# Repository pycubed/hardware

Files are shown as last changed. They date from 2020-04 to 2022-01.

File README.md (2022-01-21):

# Hardware ⚙
<br><br>
<p align="middle">
  
</p><br>

## [All PyCubed Resources](https://www.notion.so/maholli/All-PyCubed-Resources-8738cab0dd0743239a3cde30c6066452)
Tutorials, design resources, and more!
<br>

## Details:
- 4-layer PCB, minimum trace/spacing > 8 mils.
- Can be fabricated using standard FR4 for prototypes and Isola FR408HR for flight.
  - 50 ohm controlled impedance design spec'd for FR408HR with 11 mils external and 10.7 mils interal trace widths.
  - See [PyCubed's 2019 SmallSat Paper](https://github.com/pycubed/documentation/blob/master/PyCubed_smallsat-paper.pdf) for more discussion on the stack-up.
- Zipped, ready-to-order, gerber files can be found in the root of each revision directory. 
- NOTE: PyCubed layout has been ported from Eagle to KiCad to maintain the open-source nature of the project. Visit [http://www.kicad.org/](http://www.kicad.org/) for more details on this layout tool.
<br>

## Change Log
- [mainboard-v04 ➡ mainboard-v05](https://pycubed.org/v04-v05-Change-Log-7d80b1fb81be423a9da197f820e87538)
<br>

## Interactive Bill of Materials 🛒
- [mainboard-v01](https://pycubed.github.io/hardware/mainboard-v01)
- [mainboard-v02](https://pycubed.github.io/hardware/mainboard-v02)
- [mainboard-v04](https://pycubed.github.io/hardware/mainboard-v04)
- [mainboard-v05](https://pycubed.github.io/hardware/mainboard-v05)
<br>
<br>
<br>
<br>
<br>
<br>

## License
<br />
- Hardware in this repository is licensed under a <a rel="license" href="http://creativecommons.org/licenses/by-sa/4.0/">Creative Commons Attribution-ShareAlike 4.0 International License</a>.
- Software/firmware in this repository is licensed under MIT unless otherwise indicated.

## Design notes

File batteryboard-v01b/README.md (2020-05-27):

# PyCubed Battery Board 🔋

## [⭐ See the PyCubed Battery page for more details](https://www.notion.so/maholli/PyCubed-4cbfac7e9b684852a2ab2193bd485c4d)

<p align="middle">
  
</p>

2S3P Li-ion battery pack for CubeSat designs.
   - Fits 18650 cells (like the LG INR18650-MJ1)
   - Meets maximum capacity requirements of common CubeSat integrators
   - Uses components with radiation testing heritage
      - R5460x2xx for protection against
         - over-charge 
         - over-discharge
         - short-circuit
         - excess discharge-current
         - excess charge-current

Tested against the following flight requirement documents:
(the cells you use play a big role here)
   - TBA

## Interactive Bill of Materials 🛒
- [batteryboard-v01](https://pycubed.github.io/hardware/batteryboard-v01)

This board is merely a starting point for your spacecraft. Always follow the requirements set forth by your launch provider and integrator.

<br>
<br>
<br>
<br />This work is licensed under a <a rel="license" href="http://creativecommons.org/licenses/by/4.0/">Creative Commons Attribution 4.0 International License</a>.

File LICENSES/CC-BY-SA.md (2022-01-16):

Creative Commons Attribution-ShareAlike 4.0 International

Creative Commons Corporation ("Creative Commons") is not a law firm and does not provide legal services or legal advice. Distribution of Creative Commons public licenses does not create a lawyer-client or other relationship. Creative Commons makes its licenses and related information available on an "as-is" basis. Creative Commons gives no warranties regarding its licenses, any material licensed under their terms and conditions, or any related information. Creative Commons disclaims all liability for damages resulting from their use to the fullest extent possible.

Using Creative Commons Public Licenses

Creative Commons public licenses provide a standard set of terms and conditions that creators and other rights holders may use to share original works of authorship and other material subject to copyright and certain other rights specified in the public license below. The following considerations are for informational purposes only, are not exhaustive, and do not form part of our licenses.

Considerations for licensors: Our public licenses are intended for use by those authorized to give the public permission to use material in ways otherwise restricted by copyright and certain other rights. Our licenses are irrevocable. Licensors should read and understand the terms and conditions of the license they choose before applying it. Licensors should also secure all rights necessary before applying our licenses so that the public can reuse the material as expected. Licensors should clearly mark any material not subject to the license. This includes other CC-licensed material, or material used under an exception or limitation to copyright. More considerations for licensors : wiki.creativecommons.org/Considerations_for_licensors

Considerations for the public: By using one of our public licenses, a licensor grants the public permission to use the licensed material under specified terms and conditions. If the licensor's permission is not necessary for any reason–for example, because of any applicable exception or limitation to copyright–then that use is not regulated by the license. Our licenses grant only permissions under copyright and certain other rights that a licensor has authority to grant. Use of the licensed material may still be restricted for other reasons, including because others have copyright or other rights in the material. A licensor may make special requests, such as asking that all changes be marked or described.

Although not required by our licenses, you are encouraged to respect those requests where reasonable. More considerations for the public : wiki.creativecommons.org/Considerations_for_licensees

Creative Commons Attribution-ShareAlike 4.0 International Public License

By exercising the Licensed Rights (defined below), You accept and agree to be bound by the terms and conditions of this Creative Commons Attribution-ShareAlike 4.0 International Public License ("Public License"). To the extent this Public License may be interpreted as a contract, You are granted the Licensed Rights in consideration of Your acceptance of these terms and conditions, and the Licensor grants You such rights in consideration of benefits the Licensor receives from making the Licensed Material available under these terms and conditions.

Section 1 – Definitions.

    a. Adapted Material means material subject to Copyright and Similar Rights that is derived from or based upon the Licensed Material and in which the Licensed Material is translated, altered, arranged, transformed, or otherwise modified in a manner requiring permission under the Copyright and Similar Rights held by the Licensor. For purposes of this Public License, where the Licensed Material is a musical work, performance, or sound recording, Adapted Material is always produced where the Licensed Material is synched in timed relation with a moving image.
    b. Adapter's License means the license You apply to Your Copyright and Similar Rights in Your contributions to Adapted Material in accordance with the terms and conditions of this Public License.
    c. BY-SA Compatible License means a license listed at creativecommons.org/compatiblelicenses, approved by Creative Commons as essentially the equivalent of this Public License.
    d. Copyright and Similar Rights means copyright and/or similar rights closely related to copyright including, without limitation, performance, broadcast, sound recording, and Sui Generis Database Rights, without regard to how the rights are labeled or categorized. For purposes of this Public License, the rights specified in Section 2(b)(1)-(2) are not Copyright and Similar Rights.
    e. Effective Technological Measures means those measures that, in the absence of proper authority, may not be circumvented under laws fulfilling obligations under Article 11 of the WIPO Copyright Treaty adopted on December 20, 1996, and/or similar international agreements.
    f. Exceptions and Limitations means fair use, fair dealing, and/or any other exception or limitation to Copyright and Similar Rights that applies to Your use of the Licensed Material.
    g. License Elements means the license attributes listed in the name of a Creative Commons Public License. The License Elements of this Public License are Attribution and ShareAlike.
    h. Licensed Material means the artistic or literary work, database, or other material to which the Licensor applied this Public License.
    i. Licensed Rights means the rights granted to You subject to the terms and conditions of this Public License, which are limited to all Copyright and Similar Rights that apply to Your use of the Licensed Material and that the Licensor has authority to license.
    j. Licensor means the individual(s) or entity(ies) granting rights under this Public License.
    k. Share means to provide material to the public by any means or process that requires permission under the Licensed Rights, such as reproduction, public display, public performance, distribution, dissemination, communication, or importation, and to make material available to the public including in ways that members of the public may access the material from a place and at a time individually chosen by them.
    l. Sui Generis Database Rights means rights other than copyright resulting from Directive 96/9/EC of the European Parliament and of the Council of 11 March 1996 on the legal protection of databases, as amended and/or succeeded, as well as other essentially equivalent rights anywhere in the world.
    m. You means the individual or entity exercising the Licensed Rights under this Public License. Your has a corresponding meaning.

Section 2 – Scope.

    a. License grant.
        1. Subject to the terms and conditions of this Public License, the Licensor hereby grants You a worldwide, royalty-free, non-sublicensable, non-exclusive, irrevocable license to exercise the Licensed Rights in the Licensed Material to:
            A. reproduce and Share the Licensed Material, in whole or in part; and
            B. produce, reproduce, and Share Adapted Material.
        2. Exceptions and Limitations. For the avoidance of doubt, where Exceptions and Limitations apply to Your use, this Public License does not apply, and You do not need to comply with its terms and conditions.
        3. Term. The term of this Public License is specified in Section 6(a).
        4. Media and formats; technical modifications allowed. The Licensor authorizes You to exercise the Licensed Rights in all media and formats whether now known or hereafter created, and to make technical modifications necessary to do so. The Licensor waives and/or agrees not to assert any right or authority to forbid You from making technical modifications necessary to exercise the Licensed Rights, including technical modifications necessary to circumvent Effective Technological Measures. For purposes of this Public License, simply making modifications authorized by this Section 2(a)(4) never produces Adapted Material.
        5. Downstream recipients.
            A. Offer from the Licensor – Licensed Material. Every recipient of the Licensed Material automatically receives an offer from the Licensor to exercise the Licensed Rights under the terms and conditions of this Public License.
            B. Additional offer from the Licensor – Adapted Material. Every recipient of Adapted Material from You automatically receives an offer from the Licensor to exercise the Licensed Rights in the Adapted Material under the conditions of the Adapter's License You apply.
            C. No downstream restrictions. You may not offer or impose any additional or different terms or conditions on, or apply any Effective Technological Measures to, the Licensed Material if doing so restricts exercise of the Licensed Rights by any recipient of the Licensed Material.
        6. No endorsement. Nothing in this Public License constitutes or may be construed as permission to assert or imply that You are, or that Your use of the Licensed Material is, connected with, or sponsored, endorsed, or granted official status by, the Licensor or others designated to receive attribution as provided in Section 3(a)(1)(A)(i).
    b. Other rights.
        1. Moral rights, such as the right of integrity, are not licensed under this Public License, nor are publicity, privacy, and/or other similar personality rights; however, to the extent possible, the Licensor waives and/or agrees not to assert any such rights held by the Licensor to the limited extent necessary to allow You to exercise the Licensed Rights, but not otherwise.
        2. Patent and trademark rights are not licensed under this Public License.
        3. To the extent possible, the Licensor waives any right to collect royalties from You for the exercise of the Licensed Rights, whether directly or through a collecting society under any voluntary or waivable statutory or compulsory licensing scheme. In all other cases the Licensor expressly reserves any right to collect such royalties.

Section 3 – License Conditions.

Your exercise of the Licensed Rights is expressly made subject to the following conditions.

    a. Attribution.
        1. If You Share the Licensed Material (including in modified form), You must:
            A. retain the following if it is supplied by the Licensor with the Licensed Material:
                i. identification of the creator(s) of the Licensed Material and any others designated to receive attribution, in any reasonable manner requested by the Licensor (including by pseudonym if designated);
                ii. a copyright notice;
                iii. a notice that refers to this Public License;
                iv. a notice that refers to the disclaimer of warranties;

                v. a URI or hyperlink to the Licensed Material to the extent reasonably practicable;
            B. indicate if You modified the Licensed Material and retain an indication of any previous modifications; and
            C. indicate the Licensed Material is licensed under this Public License, and include the text of, or the URI or hyperlink to, this Public License.
        2. You may satisfy the conditions in Section 3(a)(1) in any reasonable manner based on the medium, means, and context in which You Share the Licensed Material. For example, it may be reasonable to satisfy the conditions by providing a URI or hyperlink to a resource that includes the required information.
        3. If requested by the Licensor, You must remove any of the information required by Section 3(a)(1)(A) to the extent reasonably practicable.
    b. ShareAlike.In addition to the conditions in Section 3(a), if You Share Adapted Material You produce, the following conditions also apply.
        1. The Adapter's License You apply must be a Creative Commons license with the same License Elements, this version or later, or a BY-SA Compatible License.
        2. You must include the text of, or the URI or hyperlink to, the Adapter's License You apply. You may satisfy this condition in any reasonable manner based on the medium, means, and context in which You Share Adapted Material.
        3. You may not offer or impose any additional or different terms or conditions on, or apply any Effective Technological Measures to, Adapted Material that restrict exercise of the rights granted under the Adapter's License You apply.

Section 4 – Sui Generis Database Rights.

Where the Licensed Rights include Sui Generis Database Rights that apply to Your use of the Licensed Material:

    a. for the avoidance of doubt, Section 2(a)(1) grants You the right to extract, reuse, reproduce, and Share all or a substantial portion of the contents of the database;
    b. if You include all or a substantial portion of the database contents in a database in which You have Sui Generis Database Rights, then the database in which You have Sui Generis Database Rights (but not its individual contents) is Adapted Material, including for purposes of Section 3(b); and
    c. You must comply with the conditions in Section 3(a) if You Share all or a substantial portion of the contents of the database.
    For the avoidance of doubt, this Section 4 supplements and does not replace Your obligations under this Public License where the Licensed Rights include other Copyright and Similar Rights.

Section 5 – Disclaimer of Warranties and Limitation of Liability.

    a. Unless otherwise separately undertaken by the Licensor, to the extent possible, the Licensor offers the Licensed Material as-is and as-available, and makes no representations or warranties of any kind concerning the Licensed Material, whether express, implied, statutory, or other. This includes, without limitation, warranties of title, merchantability, fitness for a particular purpose, non-infringement, absence of latent or other defects, accuracy, or the presence or absence of errors, whether or not known or discoverable. Where disclaimers of warranties are not allowed in full or in part, this disclaimer may not apply to You.
    b. To the extent possible, in no event will the Licensor be liable to You on any legal theory (including, without limitation, negligence) or otherwise for any direct, special, indirect, incidental, consequential, punitive, exemplary, or other losses, costs, expenses, or damages arising out of this Public License or use of the Licensed Material, even if the Licensor has been advised of the possibility of such losses, costs, expenses, or damages. Where a limitation of liability is not allowed in full or in part, this limitation may not apply to You.
    c. The disclaimer of warranties and limitation of liability provided above shall be interpreted in a manner that, to the extent possible, most closely approximates an absolute disclaimer and waiver of all liability.

Section 6 – Term and Termination.

    a. This Public License applies for the term of the Copyright and Similar Rights licensed here. However, if You fail to comply with this Public License, then Your rights under this Public License terminate automatically.
    b. Where Your right to use the Licensed Material has terminated under Section 6(a), it reinstates:
        1. automatically as of the date the violation is cured, provided it is cured within 30 days of Your discovery of the violation; or
        2. upon express reinstatement by the Licensor.
    c. For the avoidance of doubt, this Section 6(b) does not affect any right the Licensor may have to seek remedies for Your violations of this Public License.
    d. For the avoidance of doubt, the Licensor may also offer the Licensed Material under separate terms or conditions or stop distributing the Licensed Material at any time; however, doing so will not terminate this Public License.
    e. Sections 1, 5, 6, 7, and 8 survive termination of this Public License.

Section 7 – Other Terms and Conditions.

    a. The Licensor shall not be bound by any additional or different terms or conditions communicated by You unless expressly agreed.
    b. Any arrangements, understandings, or agreements regarding the Licensed Material not stated herein are separate from and independent of the terms and conditions of this Public License.

Section 8 – Interpretation.

    a. For the avoidance of doubt, this Public License does not, and shall not be interpreted to, reduce, limit, restrict, or impose conditions on any use of the Licensed Material that could lawfully be made without permission under this Public License.
    b. To the extent possible, if any provision of this Public License is deemed unenforceable, it shall be automatically reformed to the minimum extent necessary to make it enforceable. If the provision cannot be reformed, it shall be severed from this Public License without affecting the enforceability of the remaining terms and conditions.
    c. No term or condition of this Public License will be waived and no failure to comply consented to unless expressly agreed to by the Licensor.
    d. Nothing in this Public License constitutes or may be interpreted as a limitation upon, or waiver of, any privileges and immunities that apply to the Licensor or You, including from the legal processes of any jurisdiction or authority.

Creative Commons is not a party to its public licenses. Notwithstanding, Creative Commons may elect to apply one of its public licenses to material it publishes and in those instances will be considered the "Licensor." The text of the Creative Commons public licenses is dedicated to the public domain under the CC0 Public Domain Dedication. Except for the limited purpose of indicating that material is shared under a Creative Commons public license or as otherwise permitted by the Creative Commons policies published at creativecommons.org/policies, Creative Commons does not authorize the use of the trademark "Creative Commons" or any other trademark or logo of Creative Commons without its prior written consent including, without limitation, in connection with any unauthorized modifications to any of its public licenses or any other arrangements, understandings, or agreements concerning use of licensed material. For the avoidance of doubt, this paragraph does not form part of the public licenses.

Creative Commons may be contacted at creativecommons.org.

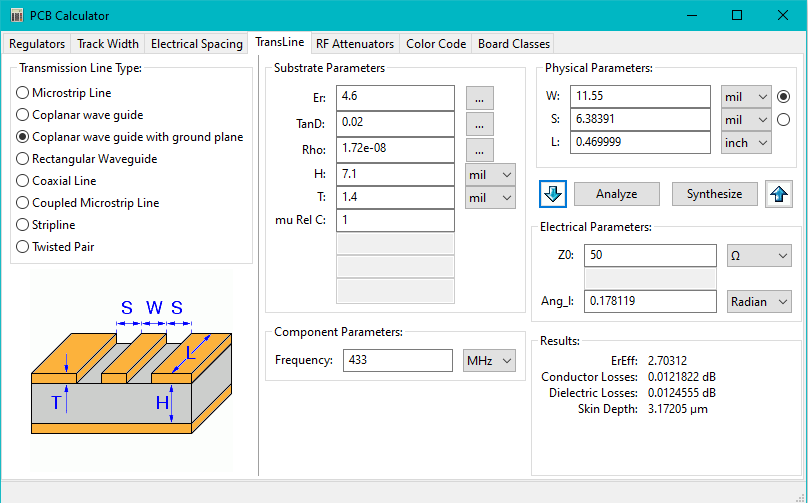
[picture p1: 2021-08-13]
mainboard-v05/stackup/stackup_outer_rf.png

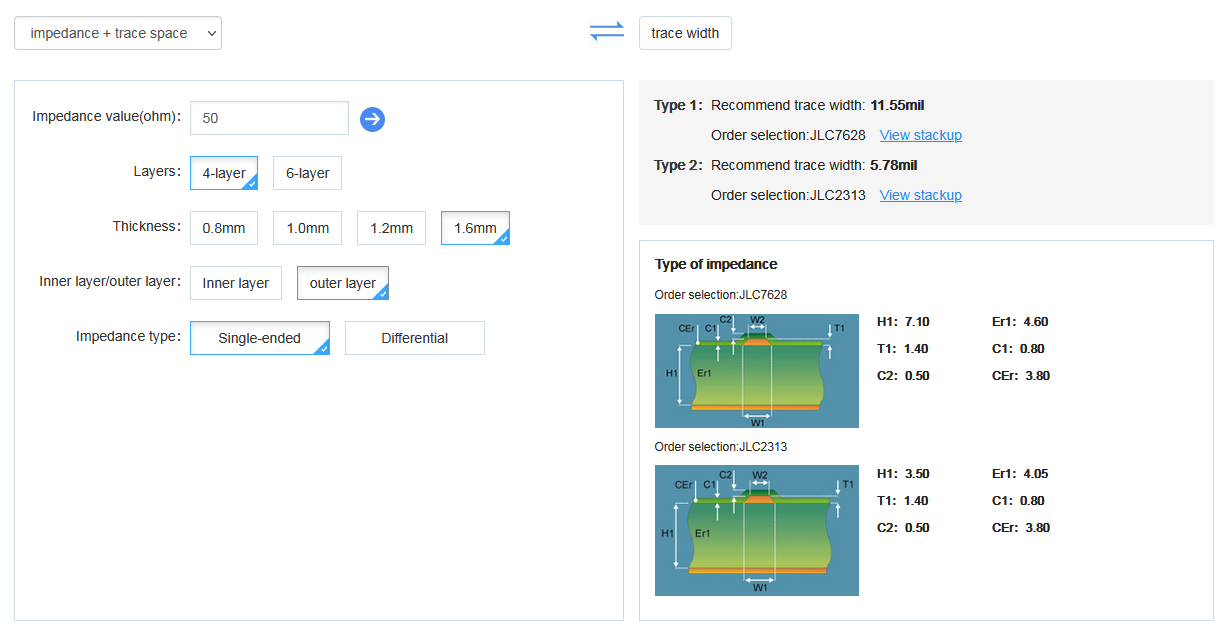
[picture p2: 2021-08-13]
mainboard-v05/stackup/stackup_outer.png

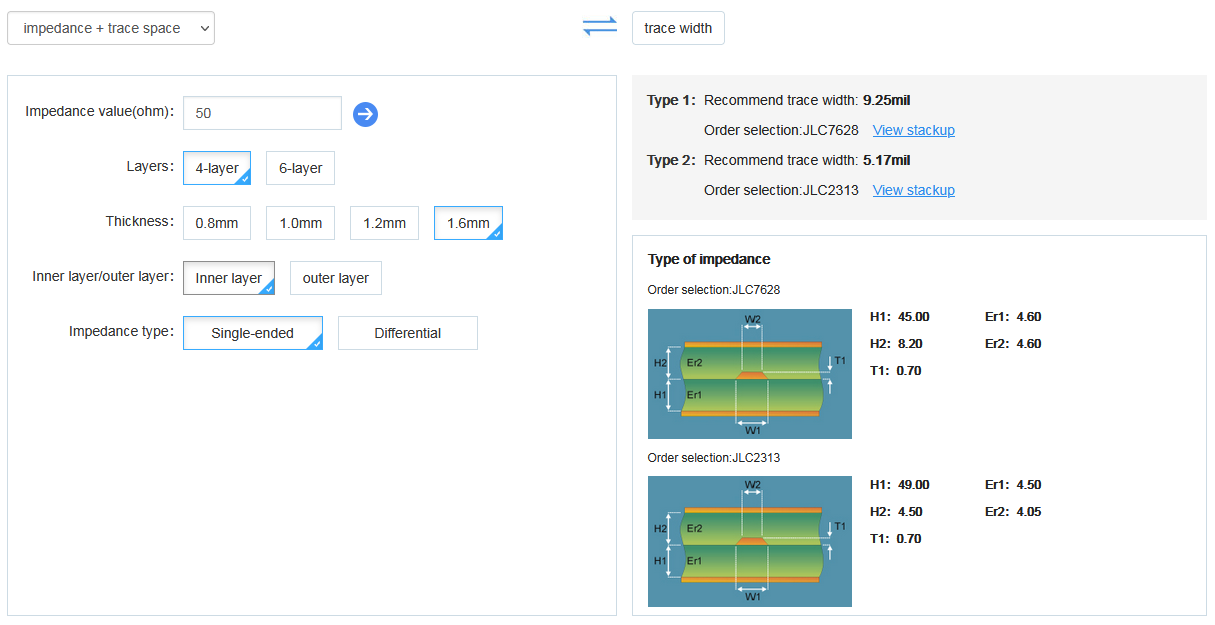
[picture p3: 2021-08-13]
mainboard-v05/stackup/stackup_inner.png

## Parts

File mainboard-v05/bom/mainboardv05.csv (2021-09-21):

Line | References | Description | Manufacturer_Name | Proto | Flight | Value | Footprint | Quantity
1 | C3, C5, C7, C9, C10, C11, C21, C24, C30, C45 | 0.1uF +-10% 50V X7R 0603 |  |  |  | 0.1uF | C_0603_1608Metric | 10
2 | C19, C20 | 100uF 16V X5R 1210 |  |  |  | 100uF | C_1210_3225Metric | 2
3 | C8, C40, C41, C42 | 10nF +-10% 50V X7R |  |  |  | 10nF | C_0603_1608Metric | 4
4 | C6, C14, C16, C22, C35, C39, C43, C44 | 10uF +-20% 10V X5R |  |  |  | 10uF | C_0603_1608Metric | 8
5 | C4, C12, C13, C15, C27, C33 | 1uF 0603 X7R |  |  |  | 1uF | C_0603_1608Metric | 6
6 | C23 | 2.2uF +-20% 6.3V X5R |  |  |  | 2.2uF | C_0603_1608Metric | 1
7 | C25 | 22nF +-10% 50V X7R |  |  |  | 22nF | C_0603_1608Metric | 1
8 | C17, C18, C28, C31, C37, C38 | 22uF +-20% 10V X5R |  |  |  | 22uF | C_0603_1608Metric | 6
9 | C26, C32 | 3.3nF +-10% 100V X7R 0603 |  |  |  | 3.3nF | C_0603_1608Metric | 2
10 | C29, C34 | 4.7uF +-20% 10V X5R |  |  |  | 4.7uF | C_0603_1608Metric | 2
11 | C36 | 47nF +-10% 50V X7R |  |  |  | 47nF | C_0603_1608Metric | 1
12 | C1, C2 | 8pF +-0.25pF 50V C0G 0603 |  |  |  | 8pF | C_0603_1608Metric | 2
13 | R10, R48, R53, R99 | 0 0603 |  |  |  | 0 | R_0603_1608Metric | 4
14 | R8 | 0.1 1% 2W 2512 |  |  |  | 0.1 | R_2512_6332Metric | 1
15 | R15, R17, R30, R37, R38, R49, R73, R74, R93, R94 | 100K 0603 |  |  |  | 100K | R_0603_1608Metric | 10
16 | R3, R4, R5, R7, R21, R24, R25, R27, R28, R31, R41, R43, R44, R45, R46, R50, R51, R52, R55, R61, R62, R66, R67, R82, R83, R84, R85 | 10K 0603 |  |  |  | 10K | R_0603_1608Metric | 27
17 | R2 | 110K 0603 |  |  |  | 110K | R_0603_1608Metric | 1
18 | R12 | 121K 0603 |  |  |  | 121K | R_0603_1608Metric | 1
19 | R26, R63, R64, R69, R70, R77, R78 | 1K 0603 |  |  |  | 1K | R_0603_1608Metric | 7
20 | R19 | 2.1M 1% 0603 |  |  |  | 2.1M | R_0603_1608Metric | 1
21 | R47, R75, R76, R95, R96 | 200K 0603 |  |  |  | 200K | R_0603_1608Metric | 5
22 | R110 | 20K 0603 |  |  |  | 20K | R_0603_1608Metric | 1
23 | R14 | 22.1K 0603 |  |  |  | 22.1K | R_0603_1608Metric | 1
24 | R20 | 3.01K 0603 |  |  |  | 3.01K | R_0603_1608Metric | 1
25 | R36 | 3.16K 0603 |  |  |  | 3.16K | R_0603_1608Metric | 1
26 | R23, R59 | 3.3K 0603 |  |  |  | 3.3K | R_0603_1608Metric | 2
27 | R35 | 30.1K 0603 |  |  |  | 30.1K | R_0603_1608Metric | 1
28 | R1 | 316K 0603 |  |  |  | 316K | R_0603_1608Metric | 1
29 | R6, R22, R32, R33, R60, R68, R92 | 4.7K 0603 |  |  |  | 4.7K | R_0603_1608Metric | 7
30 | R39, R40 | 5.1K 0603 |  |  |  | 5.1K | R_0603_1608Metric | 2
31 | R34 | 5.23K 0603 |  |  |  | 5.23K | R_0603_1608Metric | 1
32 | R71, R72, R86, R87 | 680 0603 |  |  |  | 680 | R_0603_1608Metric | 4
33 | R13, R29 | 73.2K 0603 |  |  |  | 73.2K | R_0603_1608Metric | 2
34 | R11 | 787K 0603 |  |  |  | 787K | R_0603_1608Metric | 1
35 | R16 | 845K 1% 0603 |  |  |  | 845K | R_0603_1608Metric | 1
36 | L1 | 10uH Unshielded 0805 | MicroGate | MGFL2012F100MT-LF | MGFL2012F100MT-LF | 10uH | L_0805_2012Metric_Pad1.15x1.40mm_HandSolder | 1
37 | L4 | 1uH Shielded Inductor | Prosperity Dielectrics | MCS25GD-1R0MMP | DFE252012F-1R0M | 1uH | L_2510 | 1
38 | L2 | 3.3uH Shielded Inductor | TAI-TECH | HPC5040NF-3R3MTH | SPM5030T-3R3M-HZ | 3.3uH | L_2141 | 1
39 | L3 | 33uH Shielded Inductor | 3L COILS | SNR5040K-330M | SLF6028T-330MR69-PF | 33uH | L_1812_4532Metric | 1
40 | D5 | Green LED | Lite-On Inc. | LTST-C190KGKT | LTST-C190KGKT | GREEN LED | LED_0603_1608Metric | 1
41 | D1 | RGB LED "Neopixel" | Worldsemi | WS2812B-B | WS2812B-B | WS2812B | LED_WS2812B_PLCC4_5.0x5.0mm_P3.2mm | 1
42 | D4 | Schottky Diode - 30V 1A | Diodes Incorporated | DFLS130L | DFLS130L-7 | DFLS130L | PWRDI-123 | 1
43 | U5 | 3.3V Switching Regulator | Texas Instruments | TPS54226PWPR | TPS54226PWPR | TPS54226PWPRPWP14_2P31X2P46-L | PWP14_2P31X2P46-L | 1
44 | U23 | 433 MHz 1W Radio | HopeRF | RFM98PW | RFM98PW | RFM98PW | RFM95PW | 1
45 | U16 | 5A 6V SPDT General Purpose Relay | TE Connectivity | TE Connectivity | PE014006 TE | PE014006 | RELAY_PE014006 | 1
46 | U21 | Adjustable LDO | Texas Instruments | TPS7A4501DCQT | TPS7A4501DCQT | TPS7A4501DCQT | TPS7A4501DCQT | 1
47 | U6 | Battery Charger - MPPT - Solar Input | Analog Devices Inc. | LTC4121EUD | LTC4121EUD | LTC4121 | QFN-16-PAD | 1
48 | U17 | Battery Charger - USB Power Delivery | Texas Instruments | BQ25883RGER | BQ25883RGER | BQ25883RGER | QFN50P400X400X100-25N-D | 1
49 | U7 | Fixed LDO (alt for U21 - 2021 chip shortage) | STMicroelectronics | KF50BD-TR |  | KF50BD-TR | SOIC127P600X175-8N | 1
50 | U3 | IMUs - Inertial Measurement Units 9-axis (9DOF) Absolute Orientation MEMS Sensor | Bosch Sensortec | BMX160 | BMX160 | BMX160 | BMX160 | 1
51 | U2 | Microcontroller | Microchip Technology | ATSAMD51J19A-AU | ATSAMD51J19A-AU | ATSAMD51J19A-AU | QFP50P1200X1200X120-64N | 1
52 | U8 | Non-Volatile Memory | Everspin Technologies Inc. | W25Q80DVSNIG | MR25H40MDF | MR25H40MDF | SON127P600X500X90-9N | 1
53 | U4 | Power Monitor | Analog Devices Inc. | ADM1176-1ARMZ-R7 | ADM1176-1ARMZ-R7 | ADM1176-1ARMZ-R7 | ADM1176-1ARMZ-R7 | 1
54 | U1 | Watch-dog Timer | Maxim Integrated | MAX706RESA | MAX706RESA | MAX706RESA | SO-8_3.9x4.9mm_P1.27mm | 1
55 | Y1 | 32.768kHz Crystal Oscillator | Abracon LLC | SC-32S32.768kHz20PPM7pF | ABS07-32.768KHZ-T | 32.768kHz | Crystal_SMD_3215-2Pin_3.2x1.5mm | 1
56 | SW1 | Tactile Switch SPST-NO | C&K | KMR231NG LFS | KMR231NG LFS | KMR231NG LFS | BTN_KMR2_4.6X2.8 | 1
57 | Q12, Q13, Q18, Q19 | Dual N-Channel MOSFET - 2NMOS | Diodes Incorporated | BSS138DWQ-7 | BSS138DWQ-7 | BSS138DWQ-7 | BSS138DWQ-7 | 4
58 | Q2, Q3, Q7, Q8, Q15, Q16 | Dual NPN BJT - 2NPN | ON Semiconductor | MBT2222ADW1T1G | MBT2222ADW1T1G | MBT2222ADW1T1 | SOT-363_SC-70-6 | 6
59 | Q11 | Dual PNP BJT - 2PNP | Diodes Incorporated | MMDT2907A | MMDT2907AQ-7-F | MMDT2907 | SOT-363_SC-70-6 | 1
60 | Q20, Q21, Q22 | P-Channel MOSFET | ON Semiconductor | DMP2022LSS-13 | NDS8434 | NDS8434 | NDS8434 | 3
61 | Q1, Q4 | Single N-Channel MOSFET | Infineon Technologies | 2302 | IRLML2803 | IRLML2803 | SOT-23 | 2
62 | Q5 | Single N-Channel MOSFET | ON Semiconductor | 2302 | MMBT2222AT | IRLML2803 | SOT-23 | 1
63 | Q6 | Single NPN BJT | ON Semiconductor | MMBT2222ALT1G | NSVMMBT2222ATT1G | MMBT2222AT | SOT-23 | 1
64 | Q17 | Single PNP BJT | ON Semiconductor | MMBT2907A | MMBT2907ALT1G | MMBT2907 | SOT-23 | 1
65 | J3, J4, J16, J17, J18 | 2-pin Screw Terminal - Side Entry | Phoenix Contact | 1985807 | 1985807 | 1985807 | SCREWTERMINAL-3.5MM-2_LOCK | 5
66 | J7 | Amphenol RF SMA | Amphenol | 901-144 | 901-144 | Amphenol_901-144 | SMA_Amphenol_901-144_Vertical | 1
67 | J1 | Molex microSD Card Socket | Molex | 5031821852 | 5031821852 | 503182-1852 | MOLEX_503182-1852 | 1
68 | J13 | USB Type-C Connector - Single sided | XKB Connectivity | U262-161N-4BVC11 | U262-161N-4BVC11 | USB_C_Receptacle_USB2.0 | USB_C_Receptacle_XKB_U262-161N-4BVC11 | 1

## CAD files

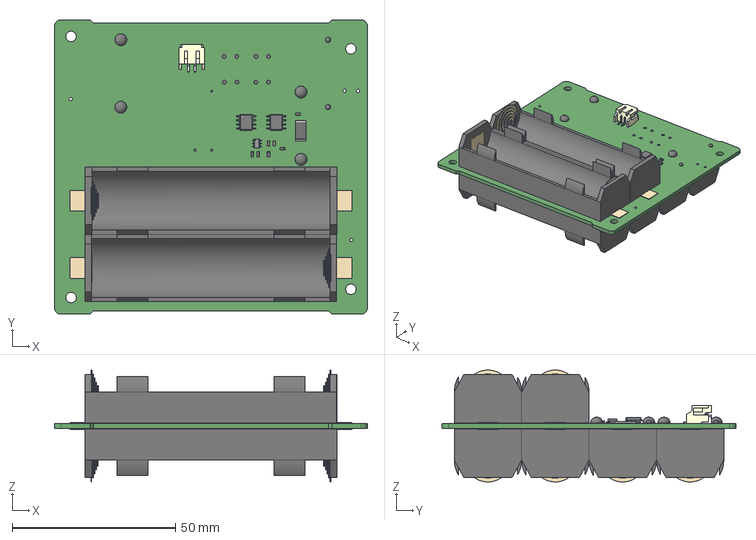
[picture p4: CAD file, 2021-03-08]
batteryboard-v01b/batteryboard.step
95.9 x 90.2 x 34.3 mm

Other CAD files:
batteryboard-v01/batteryboard.step

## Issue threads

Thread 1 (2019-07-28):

standardize SMD payload pinout?

maholli, 2019-07-28:
Payloads 1 - 4 on mainboard v01 and v02 are designed with a SPI/I2C/UART interface that accommodates my [ADC breakout boards found here](https://github.com/maholli/XTB) which have been used for a multitude of sensing/testing projects. However, the pinout is less than ideal and could be greatly improved.

## Community input needed... 💬
to narrow-in on size and pinout needs for payloads that fit this single-sided SMD criteria.

### Features I think would be helpful:
- [x] SPI, I2C, and UART communication. Current implementation requires choosing ONE of the prior communication protocols. Is there need to have parallel protocol access to a single payload?
- [ ] The SMD footprint should accommodate either a mezzanine board for payloads that are directly soldered to the mainboard as well as an SMD connector to allow for connecting the payload via a wiring harness.

### Questions for the community (feel free to respond to this issue with your specific needs!):
- power requirements?
- communication requirements?
- how many general purpose input/output (GPIO) do you need?
- what is a reasonable amount of surface area needed to accommodate your payload?
- do you need direct access to other hardware in the cubesat?

zanzeoo, 2021-01-28:
I would say an APRS link repater or a radioHam reapeter station could be cool.
I suggest to replace mechanical relay by smart switches or hotswap controllers (like LTC4367 / LTC4359 )
FPGA are more often use in space application due to a better reliability . an FPGA board with a MAX10M40 could be interesting

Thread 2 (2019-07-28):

breakout NTC to battery connector

maholli, 2019-07-28:
Battery charging circuit has (unused) temperature input capability present on some Li-Ion batteries. This should be accessible from battery terminals as well as having an enable/disable jumper (0 ohm resistor). See schematic sheet `Power.sch` for details.

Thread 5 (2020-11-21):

Recommended LoRa Ground Station Platform?

K4KDR, 2020-11-21:
Hello!

Is there a particular platform (Rasp. Pi, Arduino, ESP32, etc.) and a particular LoRa device that is recommended for compatibility with your project?

There seem to be a lot of choices in the 915 MHz LoRa world, so it would be great to obtain the best Ground Station hardware from the start to be able to support your project.

Best of luck!

-Scott,  K4KDR

elfenix7, 2021-02-24:
Hey! Know it's been a while but figured I'd chime in. I'd take a look at the Adafruit Discord, their smallsats channel has a lot of people working CubeSats, including some PyCube based ones like V3RX

K4KDR, 2021-02-24:
Thank you!  It turns out that what is now called the 'tinyGS' project has really taken off:

https://github.com/G4lile0/tinyGS

... with multiple Telegram channels in use for discussion & the posting of telemetry from their database.  It's all run via MQTT, so that  has been a fun environment to learn.

Best regards,

-Scott

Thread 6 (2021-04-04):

Add release tags for versions of PyCubed/Battery Board

polygnomial, 2021-04-04:
# Rationale
We realized we'd been using a slightly older version of v04 with some slight differences from most of the documentation. It would make life a lot easier to have a single source of truth release tag so that it is clear exactly which version is in use. This could also be extended beyond v1/2/4 to subversions. I'd be happy to submit a PR, though I'm not entirely sure how/whether release tags work in PRs.

polygnomial, 2021-04-04:
I'd be happy to submit a PR, though I'm not entirely sure how/whether release tags work in PRs.

maholli, 2021-05-03:
Yes, absolutely! I think SSI had access to v04 as it was in development and that's why you ended up with a different rev.

When I roll out v5 (coming soon!!) I'll make sure to tag it with the appropriate release.

polygnomial, 2021-05-03:
😊🛰

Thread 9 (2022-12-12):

Obsolete components

Balinerd, 2022-12-12:
I recently started sourcing some of components for a test board and fount that the BMX160 used for the IMU is no longer available for purchase.

mlyle, 2022-12-12:
https://www.lcsc.com/search?q=bmx160  LCSC still has a few, but this is admittedly a problem.

mlyle, 2022-12-13:
I'm not a project maintainer, etc.. just a user.

There's not a replacement to the bmx160 in the same footprint, AFAIK.  And, the bigger issue is, BMX160 has flight heritage, where most of the replacements would not.

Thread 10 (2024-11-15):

Interactive Bill of Materials

PowerfulTitan, 2024-11-15:
Hello!

I am building some battery boards for my college's cubesat team. The links to the interactive bill of materials appear to be broken; I was wondering if this was available somewhere else or if there was a way I could view it?

maholli, 2024-11-15:
Hi yeah the website has been having trouble and I haven't had the chance to fix it.

The github repos still have all the info you're needing, though. If you're looking for the battery board (v01b) BOM, [download this file](https://github.com/pycubed/hardware/blob/master/batteryboard-v01b/bom/index.html) (if you don't want to clone the repo) and open it with your browser.

Let me know if it doesn't work.

maholli, 2024-11-16:
yep that link in the previous message is the interactive BOM html file. Download the file and open it in your browser to see where things go.

PowerfulTitan, 2024-11-16:
It worked, thank you!

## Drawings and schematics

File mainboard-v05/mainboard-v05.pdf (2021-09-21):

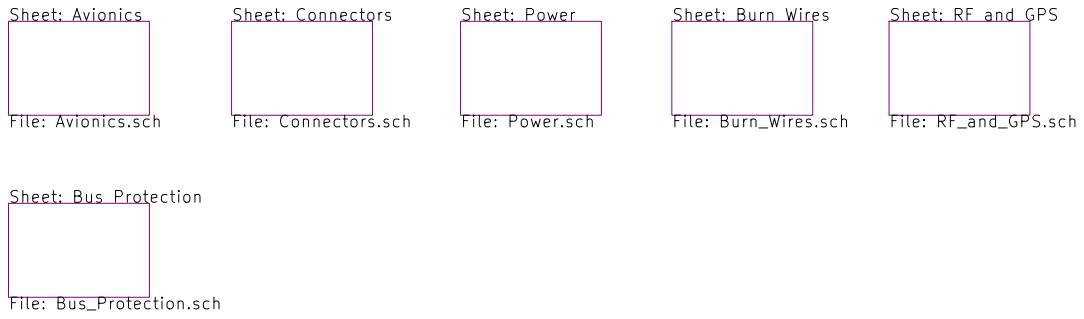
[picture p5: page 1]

Sheet: RF and GPS

File: mainboard.sch Sheet: / Max Holliday

Id: 1/7 Title: PyCubed Mainboard

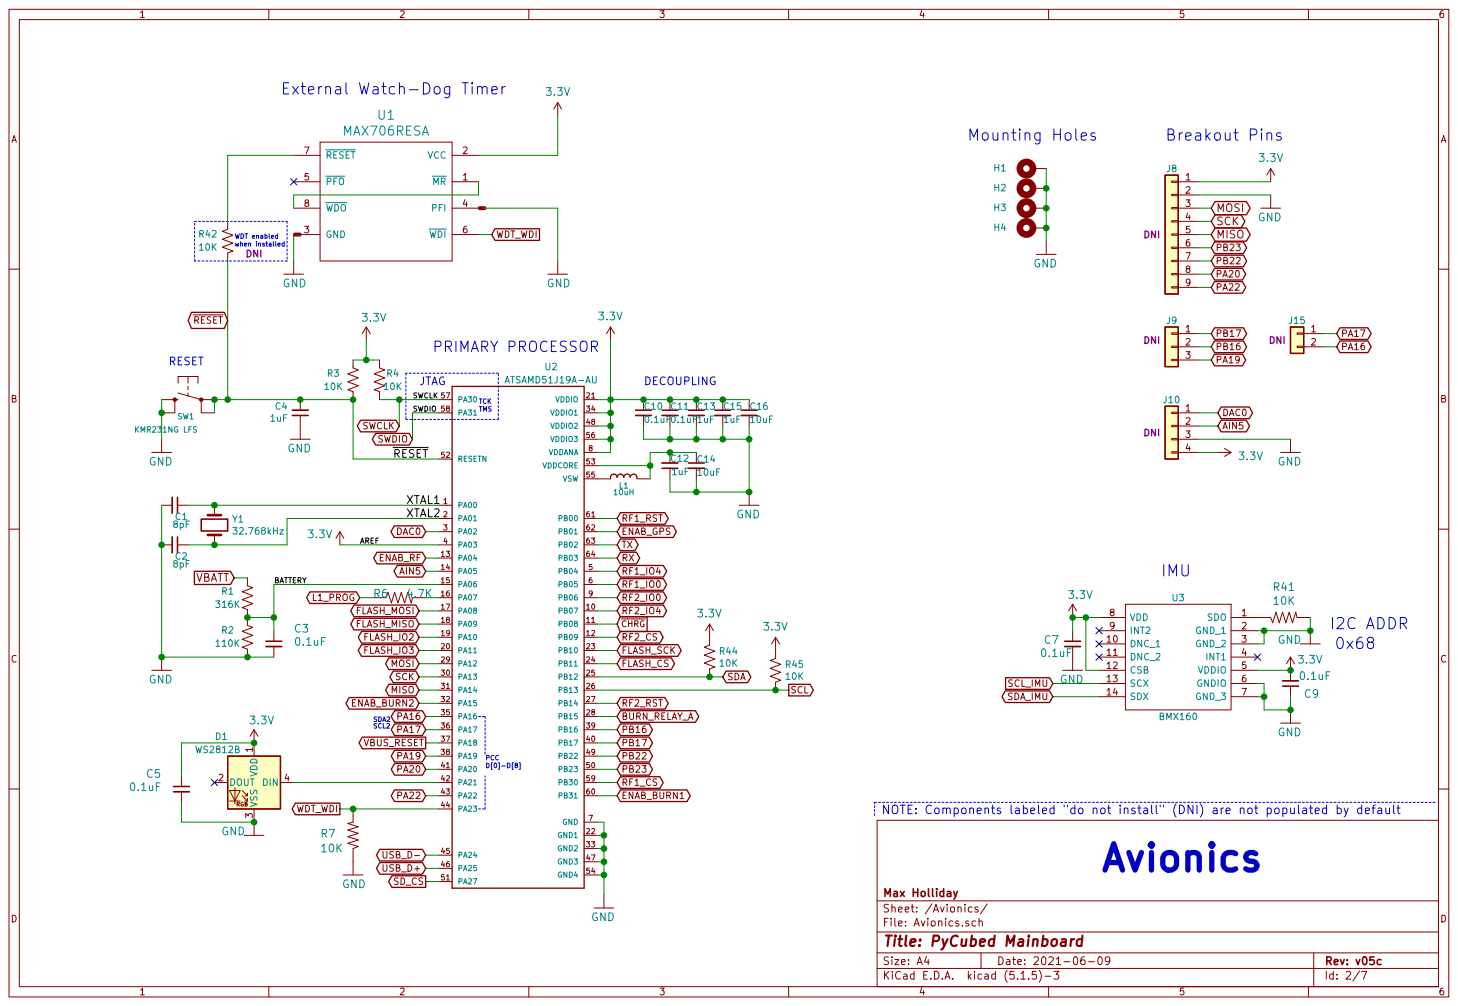
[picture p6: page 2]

NOTE: Components labeled "do not install" (DNI) are not populated by default

File: Avionics.sch Sheet: /Avionics/ Max Holliday

Id: 2/7 Title: PyCubed Mainboard

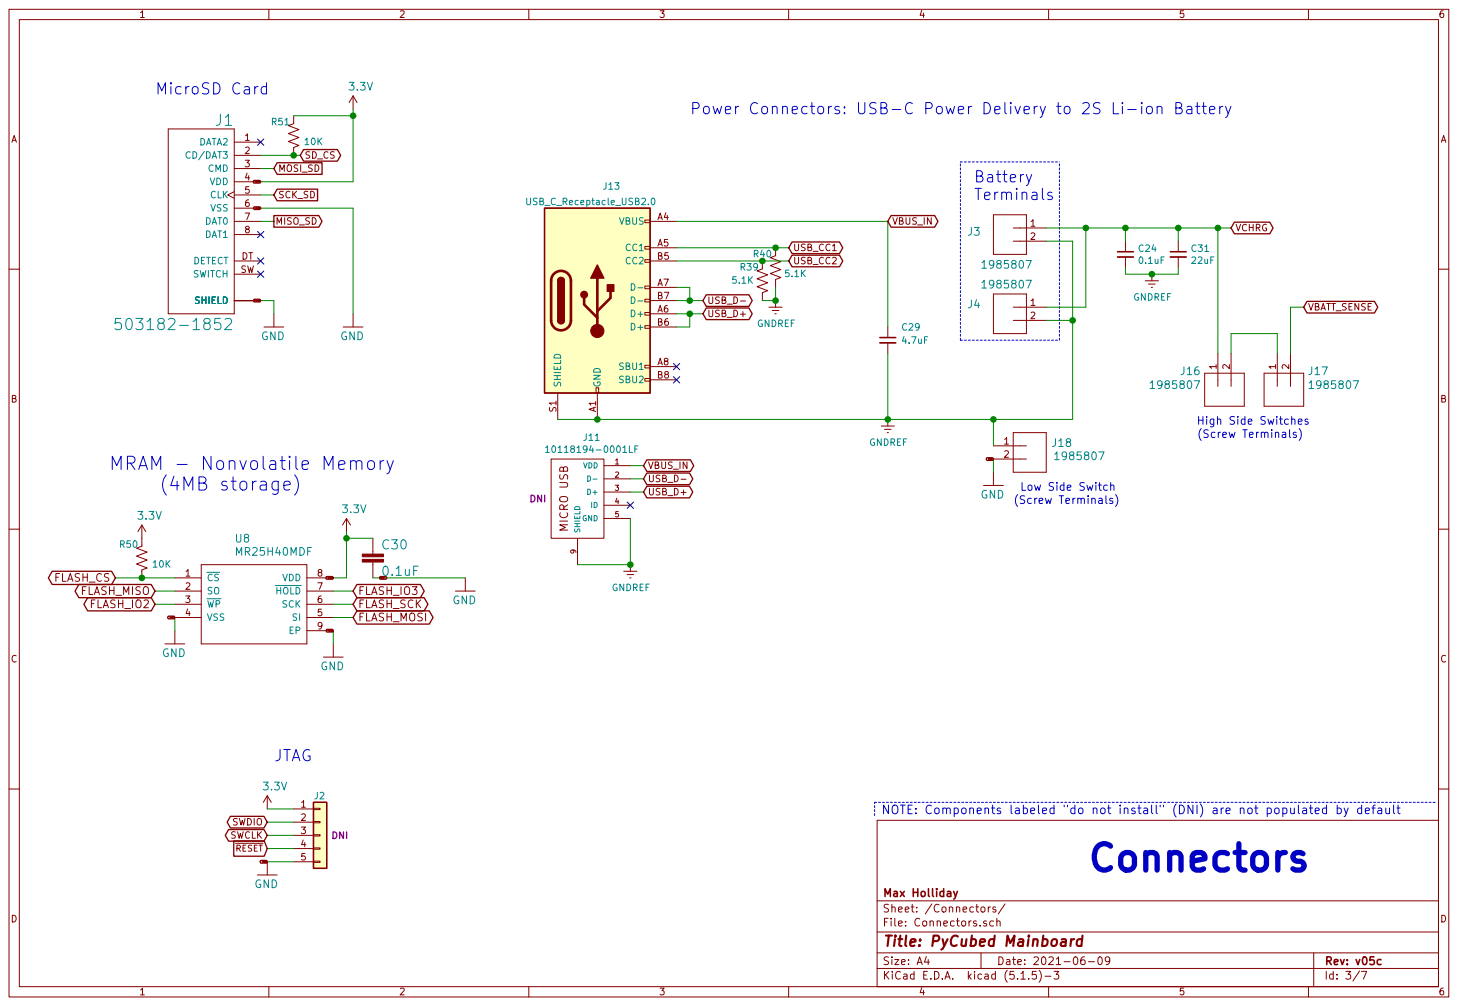
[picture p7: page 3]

Power Connectors: USB-C Power Delivery to 2S Li-ion Battery

NOTE: Components labeled "do not install" (DNI) are not populated by default

Id: 3/7 Title: PyCubed Mainboard

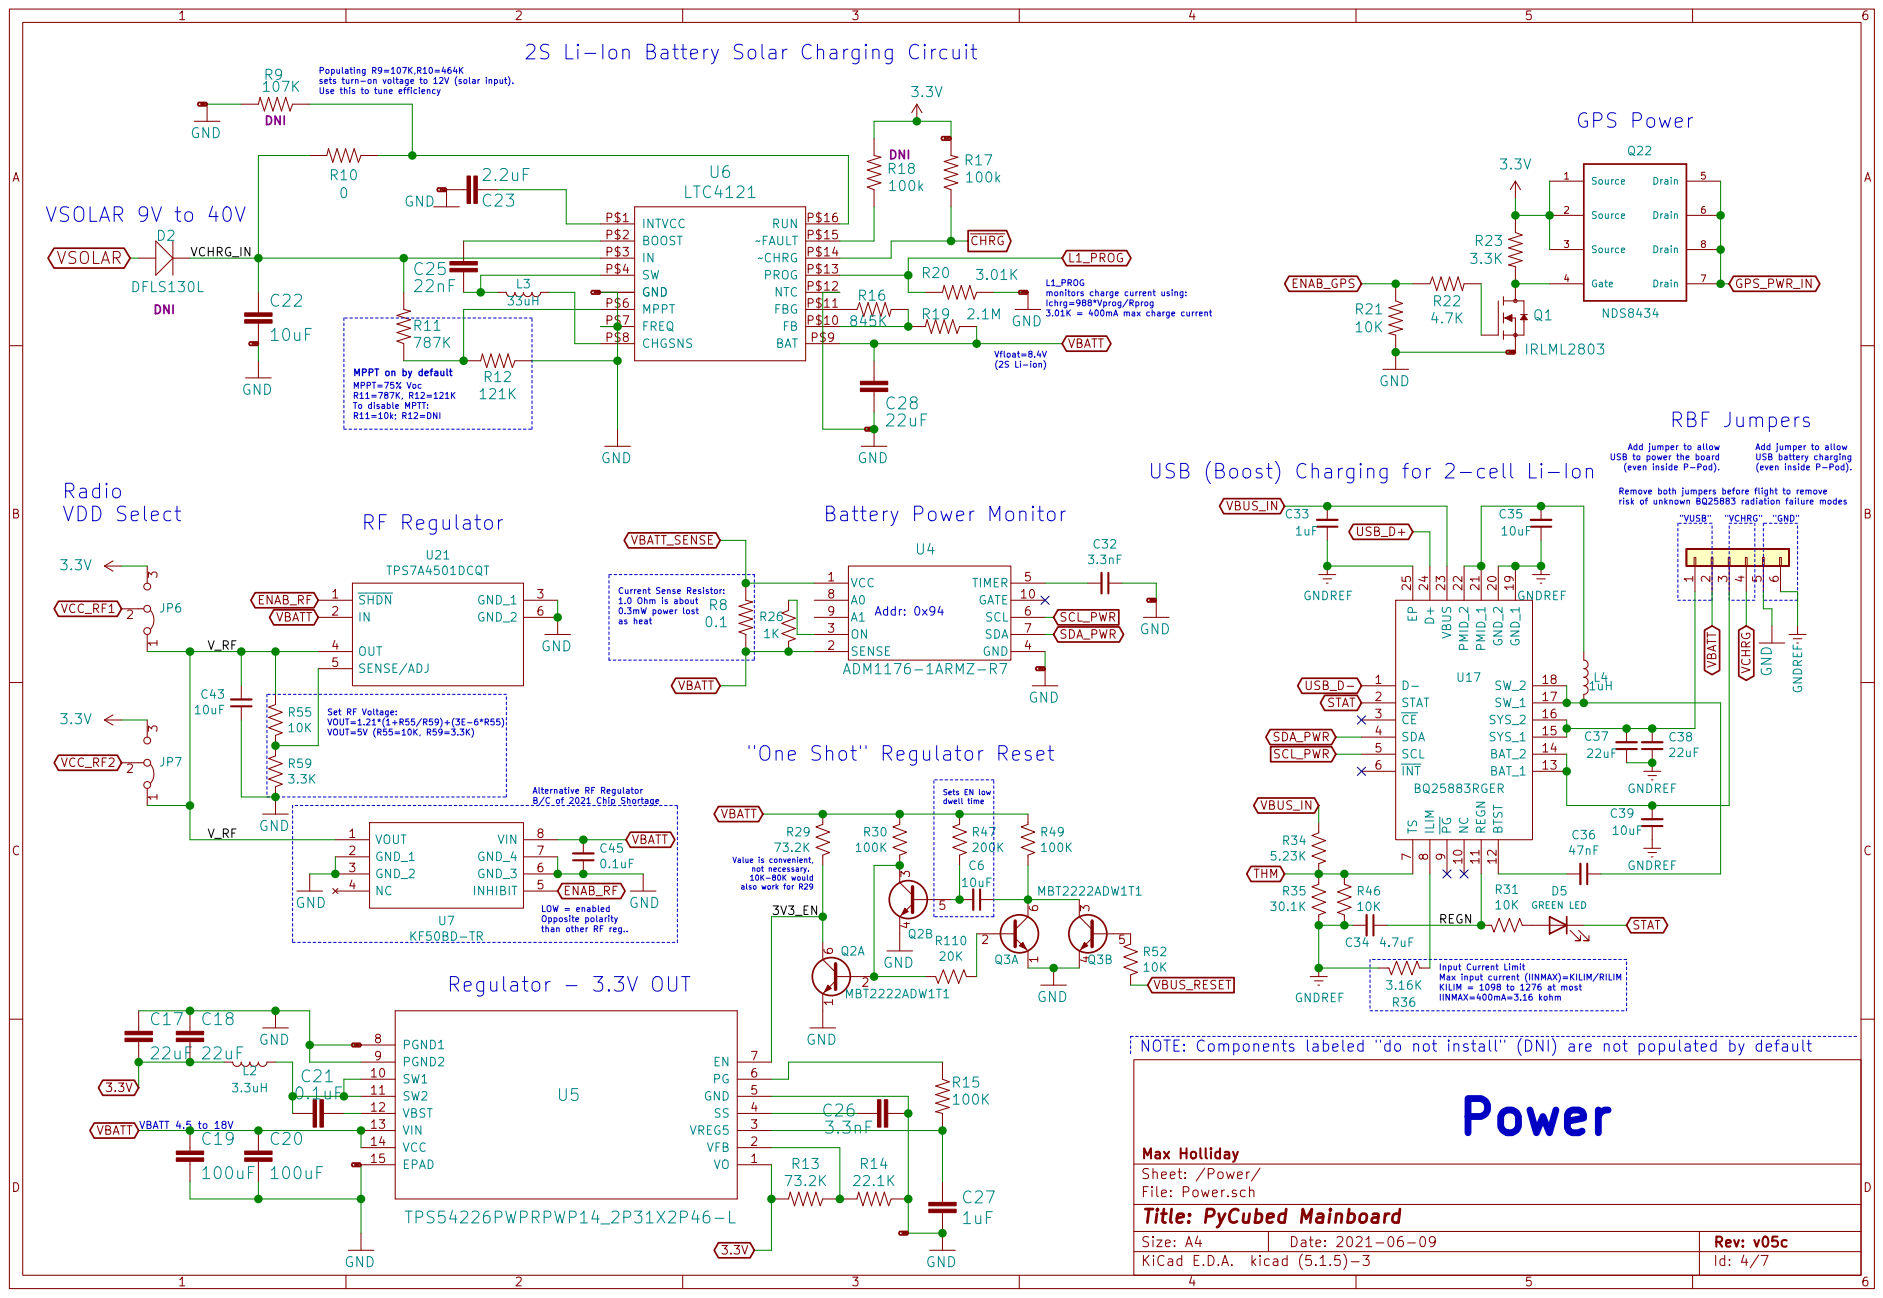
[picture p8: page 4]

L1_PROG
L1_PROG monitors charge current using:
Ichrg=988*Vprog/Rprog
3.01K = 400mA max charge current

To disable MPTT: R11=10k; R12=DNI MPPT on by default
risk of unknown BQ25883 radiation failure modes MPPT=75% Voc R11=787K, R12=121K

Add jumper to allow
USB to power the board

USB battery charging

(even inside P-Pod). RF Regulator

dwell time "One Shot" Regulator Reset

Alternative RF Regulator B/C of 2021 Chip Shortage

LOW = enabled Opposite polarity

Input Current Limit Max input current (IINMAX)=KILIM/RILIM

KILIM = 1098 to 1276 at most
IINMAX=400mA=3.16 kohm

Id: 4/7 Title: PyCubed Mainboard

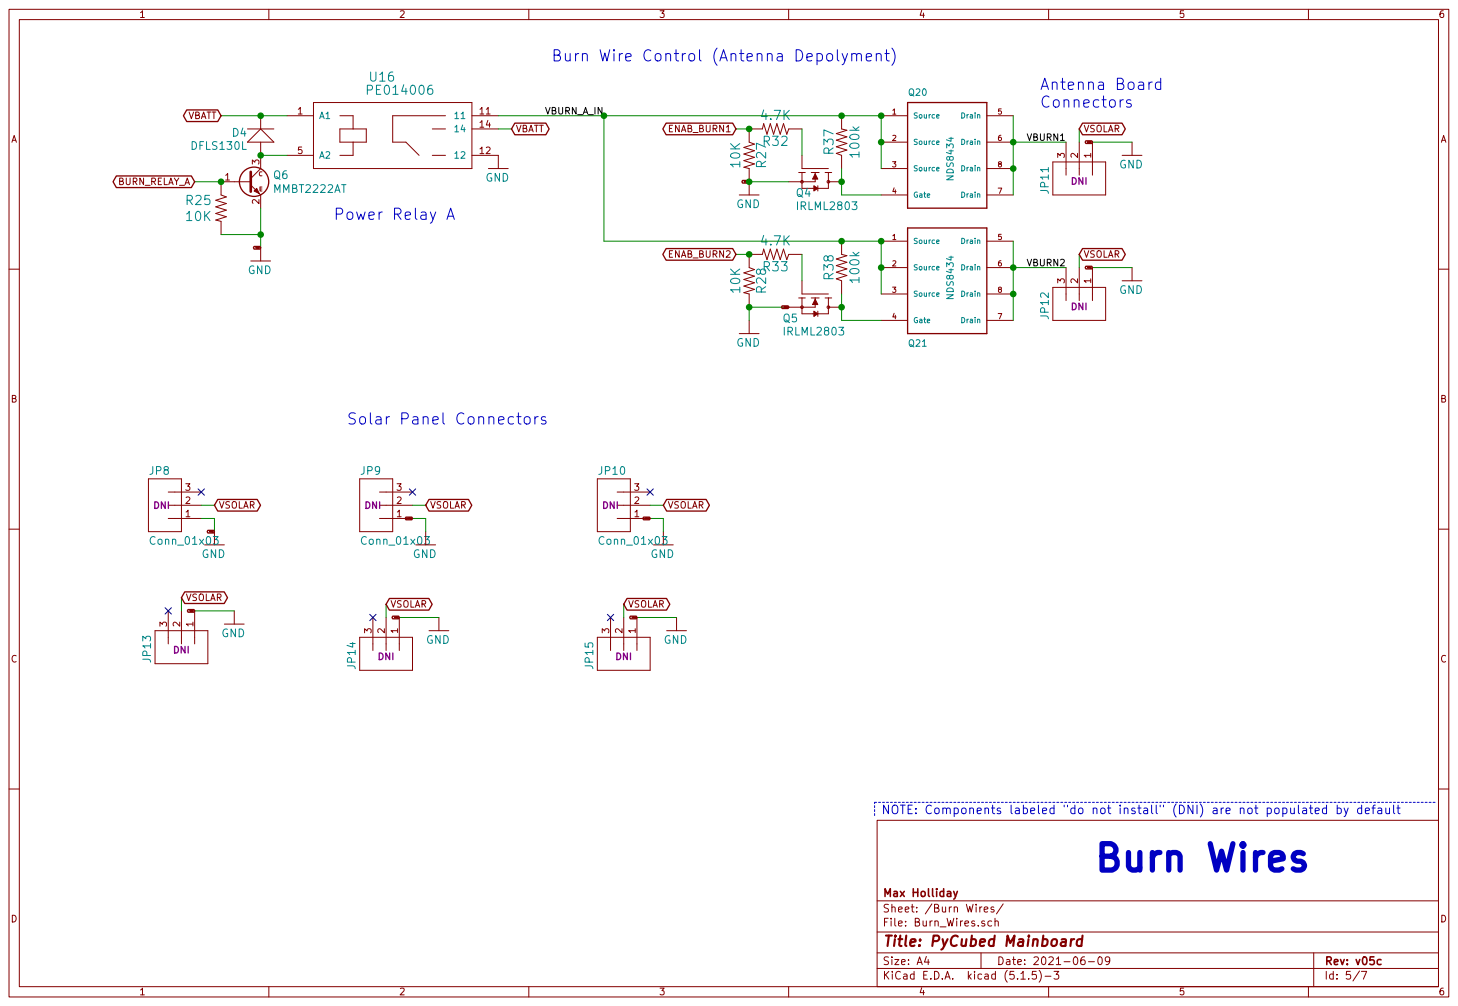
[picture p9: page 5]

Burn Wire Control (Antenna Depolyment)

1 JP14 DNI GND GND GND GND GND GND GND

GND
File: Burn_Wires.sch Sheet: /Burn Wires/ Max Holliday GND

NOTE: Components labeled "do not install" (DNI) are not populated by default

Id: 5/7 Title: PyCubed Mainboard

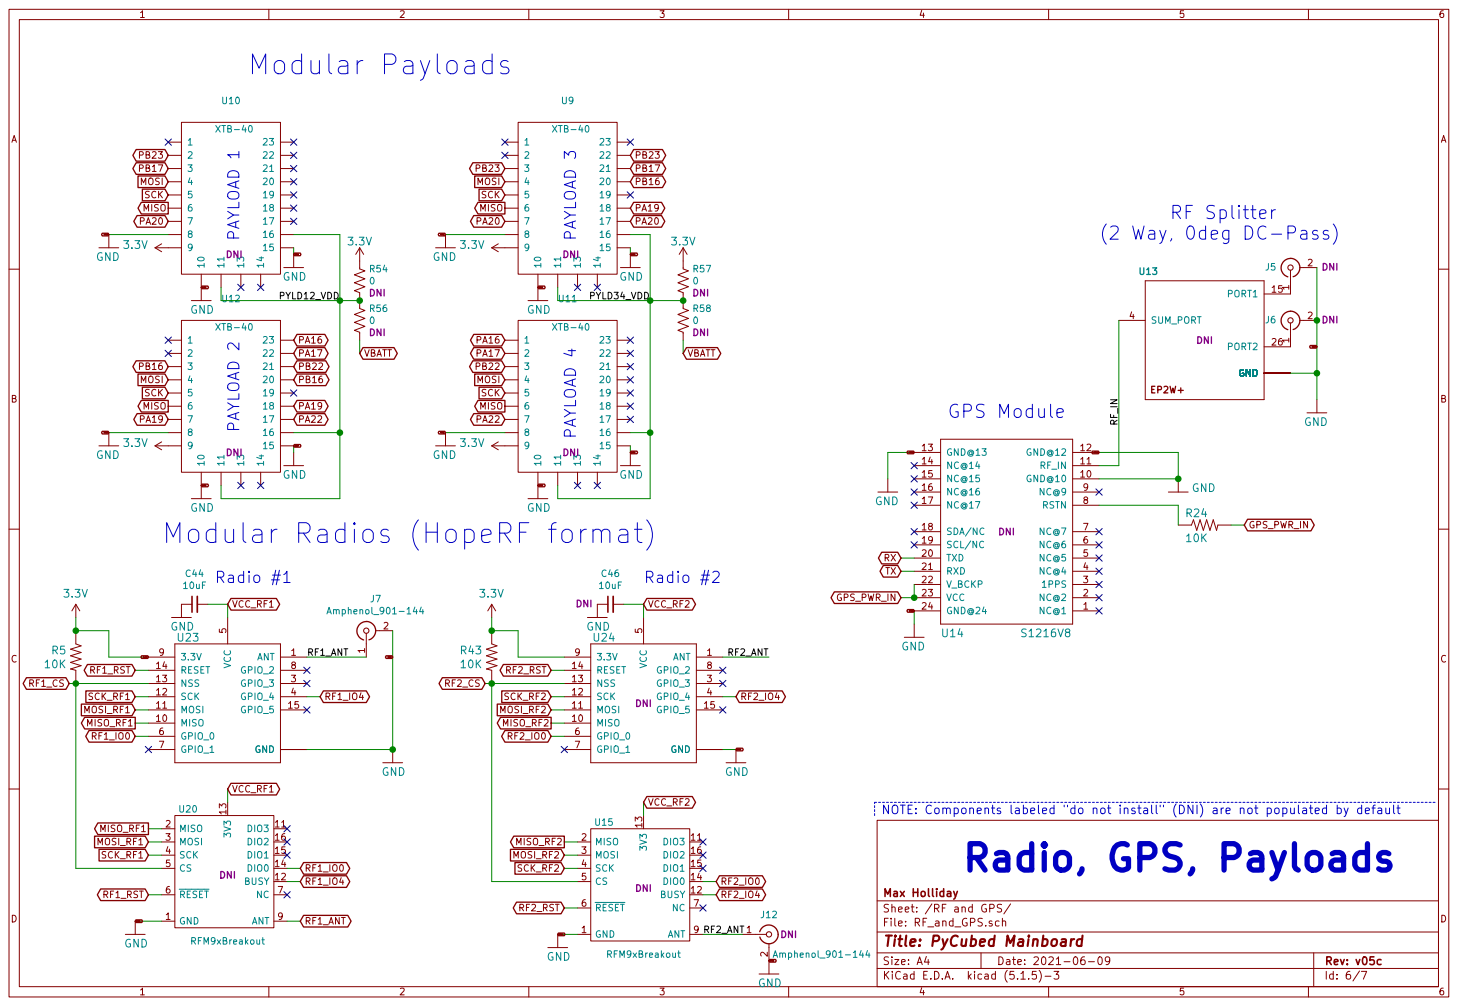
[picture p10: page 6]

Modular Radios (HopeRF format)

5 ANT 1 MISO 10 MOSI 11 SCK 12 NSS 13 RESET 14 GPIO_5 15 GND GPIO_3 3 GPIO_4 4 GPIO_0 6 GPIO_1 7 GPIO_2 8

NOTE: Components labeled "do not install" (DNI) are not populated by default

File: RF_and_GPS.sch Sheet: /RF and GPS/ Max Holliday

Id: 6/7 Title: PyCubed Mainboard

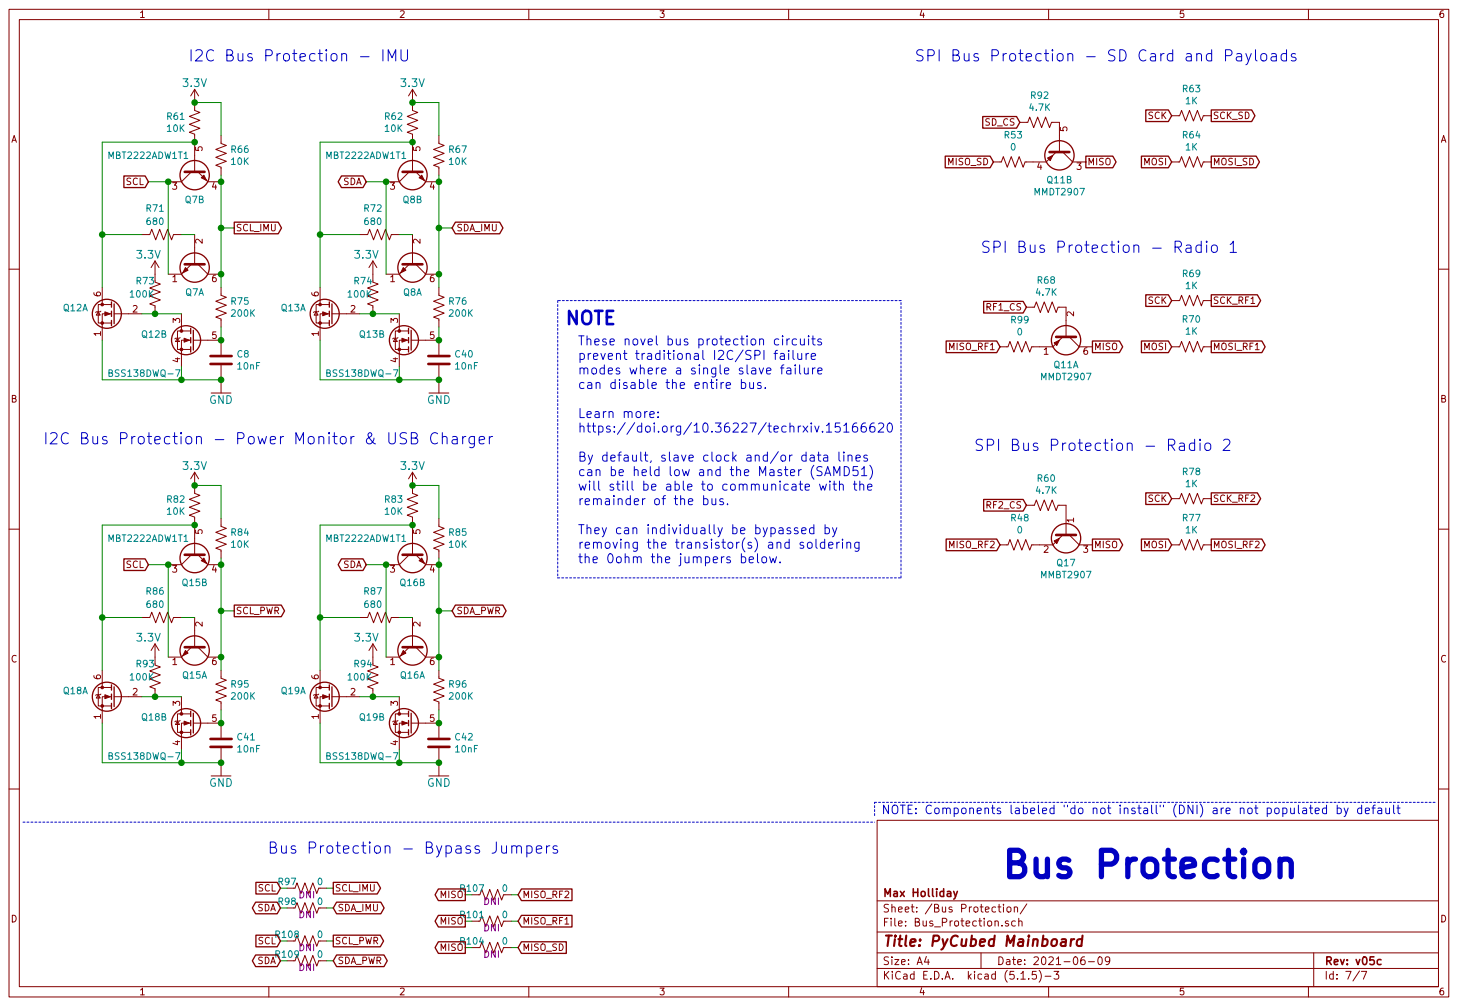
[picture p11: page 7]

SPI Bus Protection - Radio 1

NOTE
These novel bus protection circuits
prevent traditional I2C/SPI failure
modes where a single slave failure
can disable the entire bus.

Learn more:
https://doi.org/10.36227/techrxiv.15166620

By default, slave clock and/or data lines
can be held low and the Master (SAMD51)
will still be able to communicate with the
remainder of the bus.

They can individually be bypassed by
removing the transistor(s) and soldering
the 0ohm the jumpers below.

NOTE: Components labeled "do not install" (DNI) are not populated by default
Bus Protection

Bus Protection - Bypass Jumpers

Id: 7/7 Title: PyCubed Mainboard

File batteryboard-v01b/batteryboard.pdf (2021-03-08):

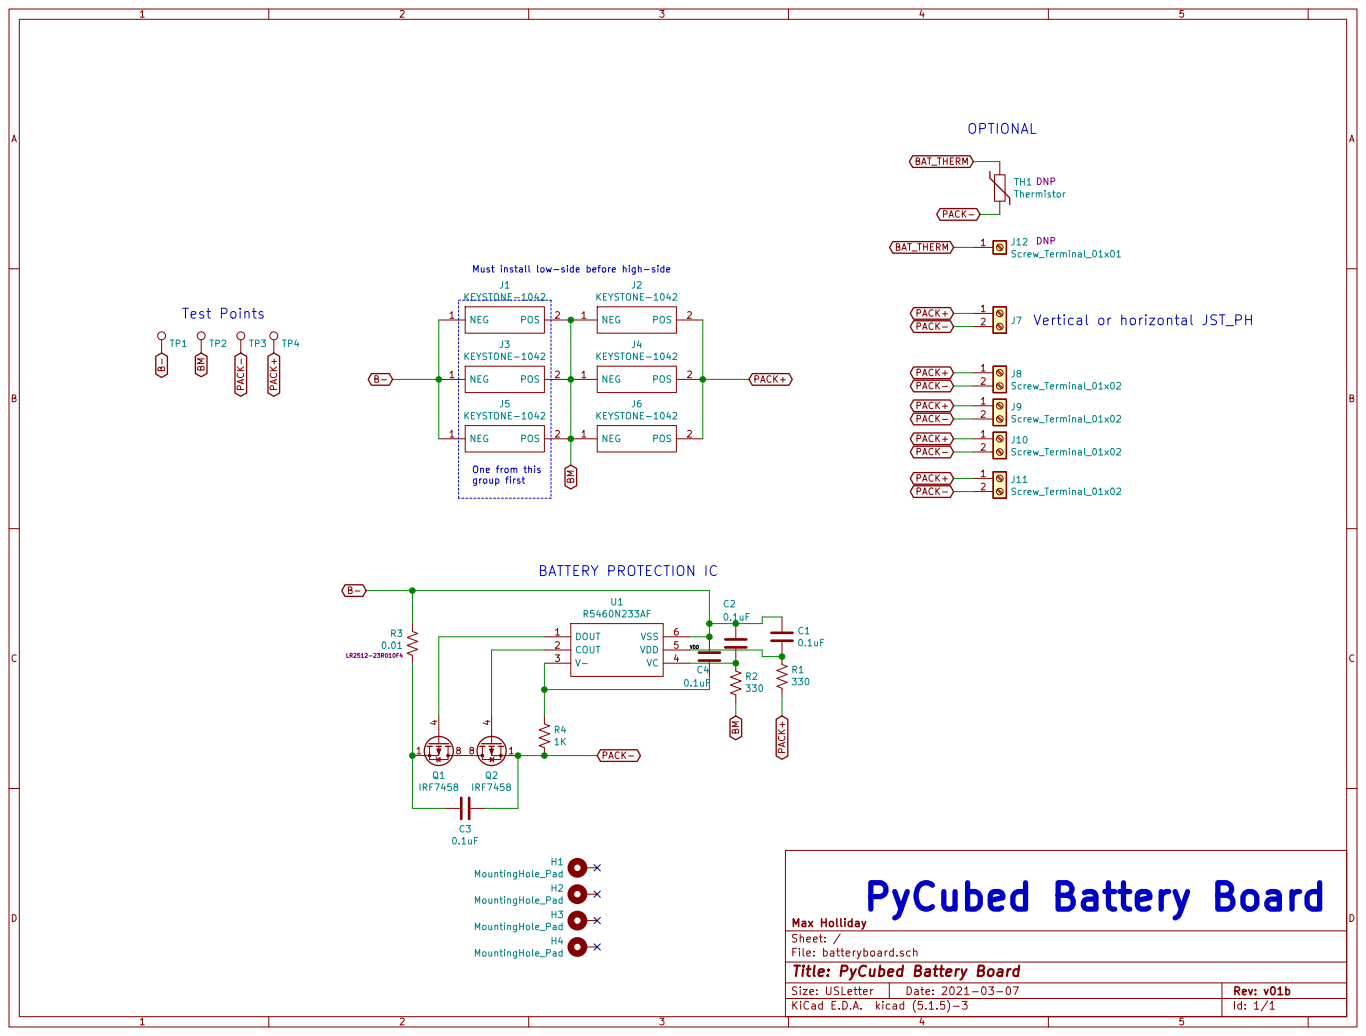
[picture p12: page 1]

Must install low-side before high-side

VDD One from this group first

File: batteryboard.sch Sheet: / Max Holliday

Id: 1/1 Title: PyCubed Battery Board

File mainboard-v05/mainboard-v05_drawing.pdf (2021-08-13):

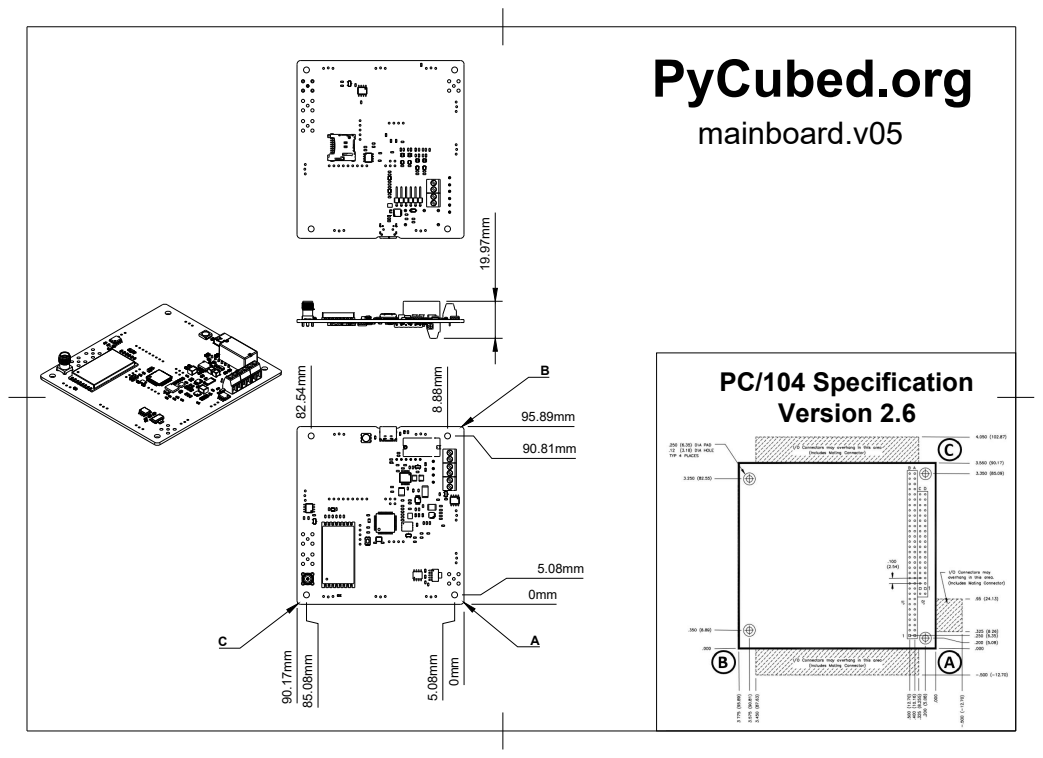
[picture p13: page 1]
PC/104 Specification Version 2.6

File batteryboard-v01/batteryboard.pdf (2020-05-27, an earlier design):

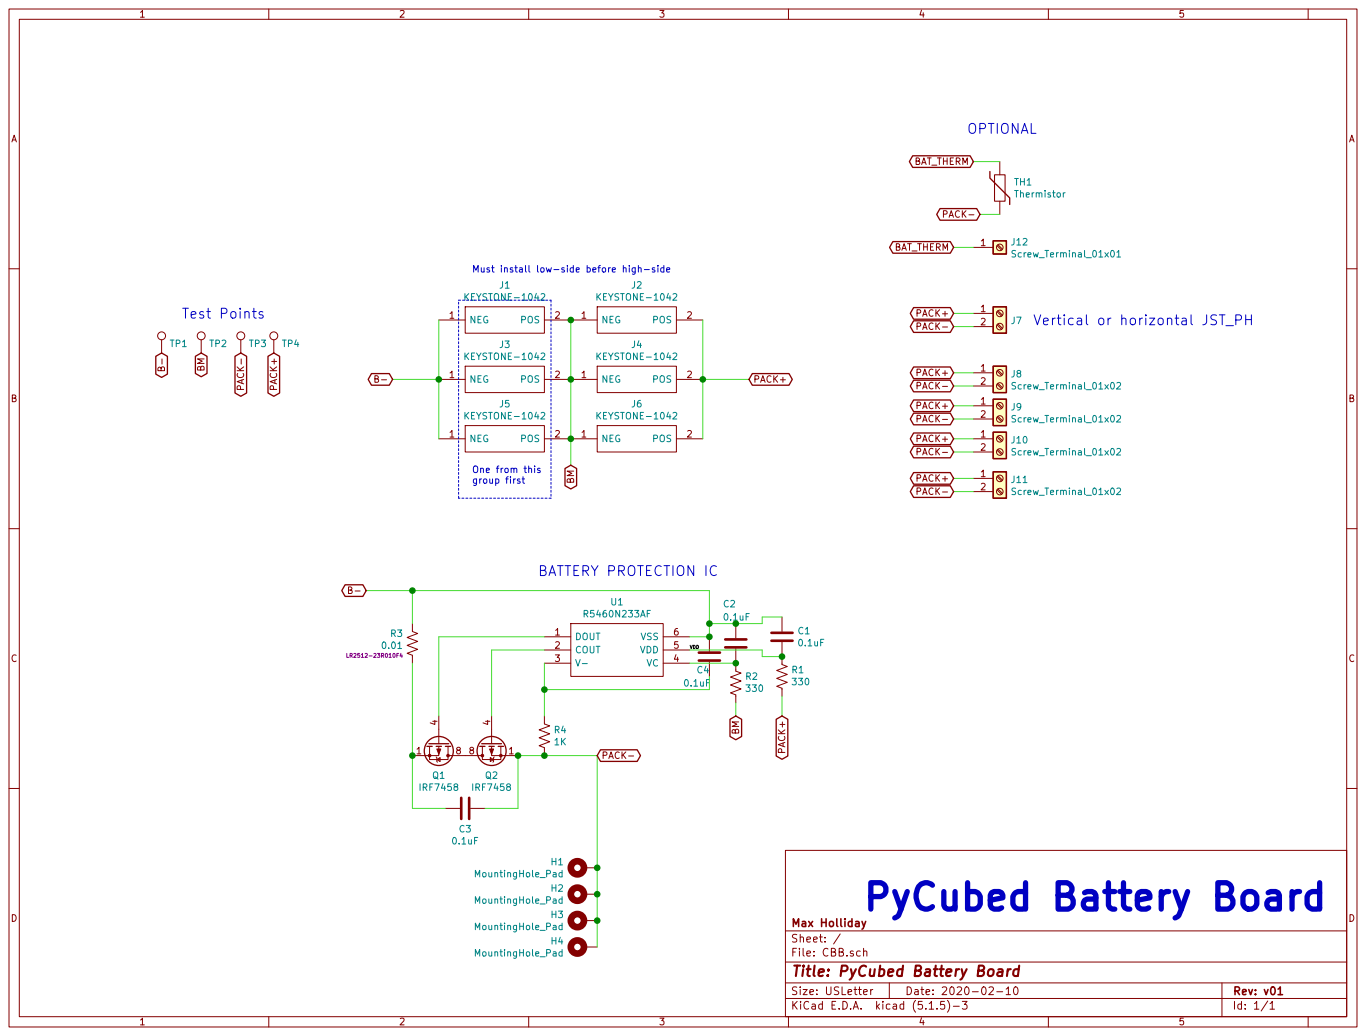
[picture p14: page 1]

Must install low-side before high-side

PACK+ PACK- PACK+ PACK- PACK- PACK+

File: CBB.sch Sheet: / Max Holliday

Id: 1/1 Title: PyCubed Battery Board

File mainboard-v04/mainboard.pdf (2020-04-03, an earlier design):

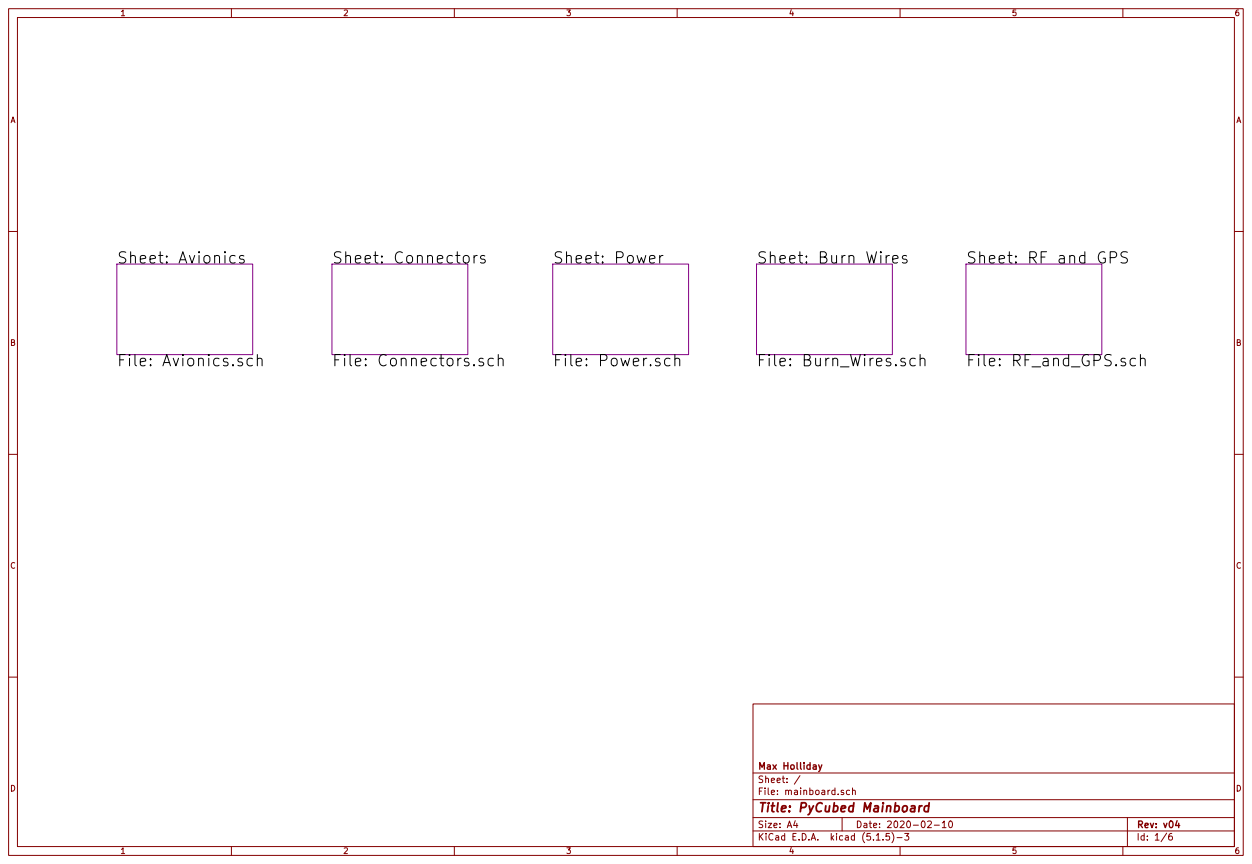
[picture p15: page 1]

Sheet: RF and GPS

File: mainboard.sch Sheet: / Max Holliday

Id: 1/6 Title: PyCubed Mainboard

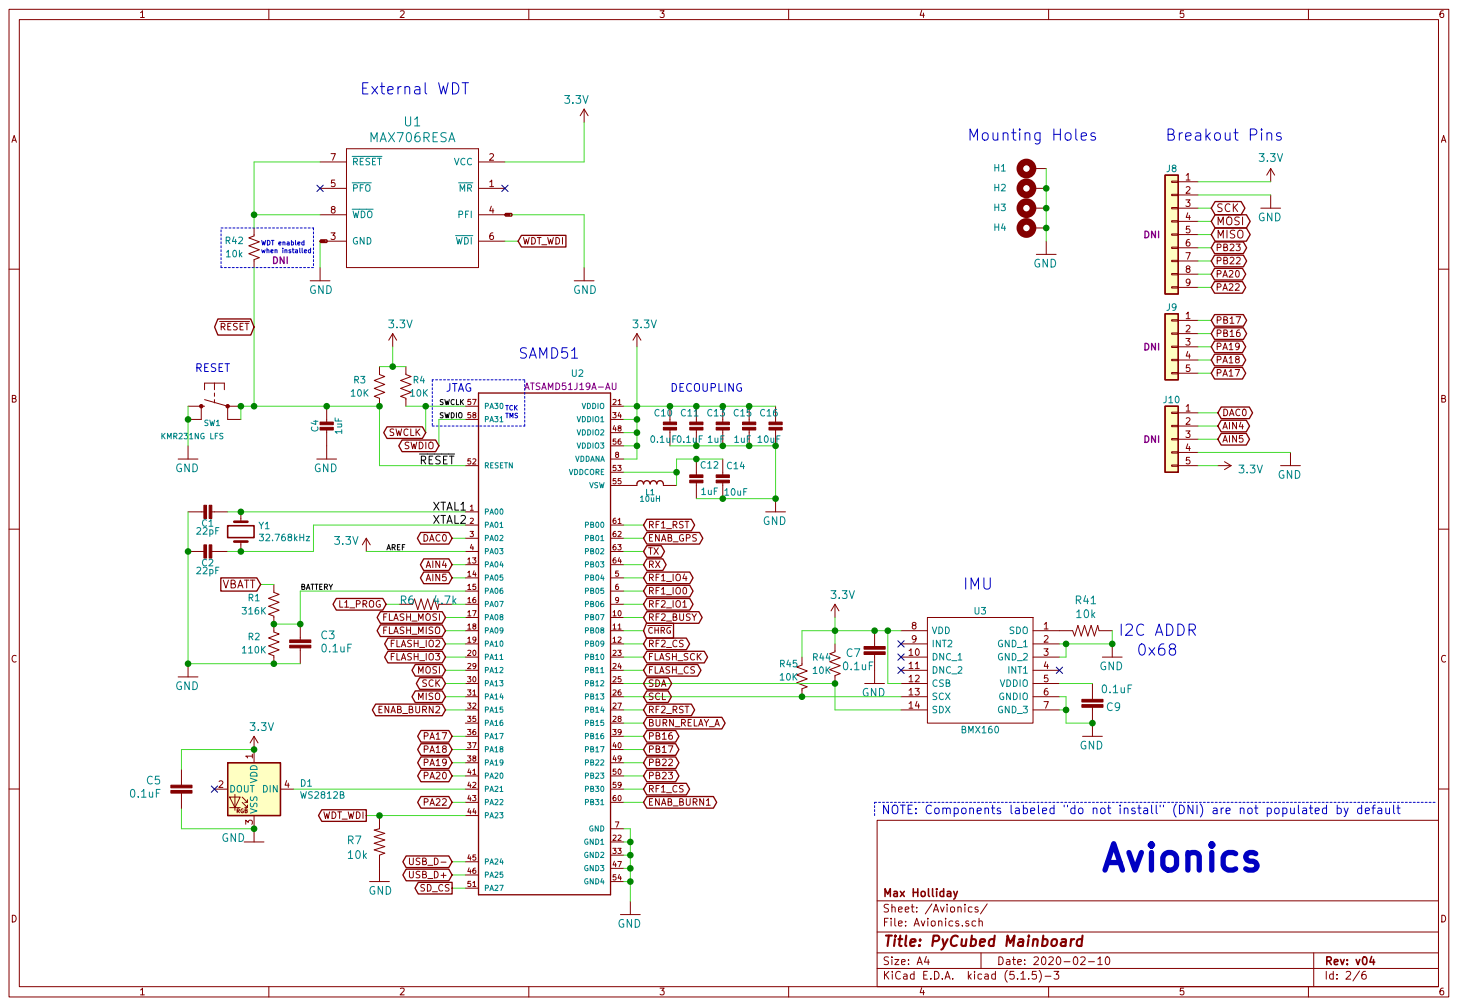
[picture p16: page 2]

TMS WDT enabled when installed RESET
GND GND

SWDIO | 1uF | C15 1uF | C16

TCK

File: Avionics.sch Sheet: /Avionics/ Max Holliday

Id: 2/6 Title: PyCubed Mainboard


VBATT Power Connectors: USB-C Power Delivery to 2S Li-ion Battery

NOTE: Components labeled "do not install" (DNI) are not populated by default

File: Connectors.sch Sheet: /Connectors/ Max Holliday

Id: 3/6 Title: PyCubed Mainboard


(only install this if you know what you're doing!) 2s2P Li-Ion Battery Solar Charging Circuit

L1_PROG monitors charge current using:

3.01K = 400mA max charge current Current Sense Resistor: 1.0 Ohm is about 0.3mW

MPPT off by default To enable: MPPT=75% Voc R11=787K, R12=121K

USB (Boost) Charging for 2-cell Li-Ion

"VCHRG" Add jumper to allow
USB to power the board

(even inside P-Pod). Addr: 0x94 System Power Monitor

risk of unknown BQ25883 radiation failure modes NOTE: Components labeled "do not install" (DNI) are not populated by default

File: Power.sch Sheet: /Power/ Max Holliday R8
D5 GREEN LED GND

In the case of U5 failure, U4 can disable
regulator based on TIMER capacitor

Id: 4/6 Title: PyCubed Mainboard


Burn Wire Control (Antenna Depolyment)

NOTE: Components labeled "do not install" (DNI) are not populated by default

File: Burn_Wires.sch Sheet: /Burn Wires/ Max Holliday

Id: 5/6 Title: PyCubed Mainboard


File: RF_and_GPS.sch Sheet: /RF and GPS/ Max Holliday GND

Modular Radios (HopeRF format)
0 GND

Optional VCC input for Radio #1
(if separate than 3V3, DNI R48)

5 ANT 1 MISO 10 MOSI 11 SCK 12 NSS 13 RESET 14 GPIO_5 15 GND GPIO_3 3 GPIO_4 4 GPIO_0 6 GPIO_1 7 GPIO_2 8

NOTE: Components labeled "do not install" (DNI) are not populated by default
Radio, GPS, Payloads

Id: 6/6 Title: PyCubed Mainboard

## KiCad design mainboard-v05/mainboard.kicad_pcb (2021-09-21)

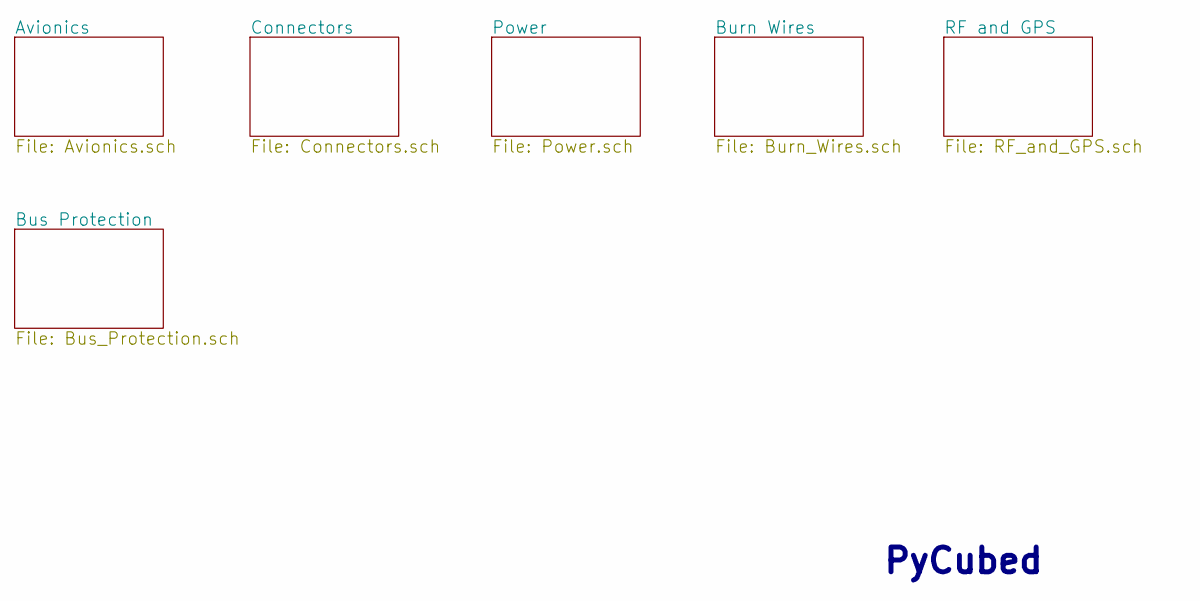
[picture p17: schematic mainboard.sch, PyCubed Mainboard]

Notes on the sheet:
PyCubed

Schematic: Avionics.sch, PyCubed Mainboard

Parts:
C1, C2: 8pF; C_0603_1608Metric
C3, C5, C7, C9, C10, C11: 0.1uF; C_0603_1608Metric
C4, C12, C13, C15: 1uF; C_0603_1608Metric
C14, C16: 10uF; C_0603_1608Metric
D1: WS2812B; LED_WS2812B_PLCC4_5.0x5.0mm_P3.2mm; Manufacturer_Part_Number WS2812B-B
H1, H2, H3, H4: MountingHole_Pad; MountingHole_3.2mm_M3_DIN965_Pad
J8: Conn_01x09; PinHeader_1x09_P2.54mm_Vertical
J9: Conn_01x03; PinHeader_1x03_P2.54mm_Vertical
J10: Conn_01x04; PinHeader_1x04_P2.54mm_Vertical
J15: Conn_01x02; PinHeader_CUSTOM3
L1: 10uH; L_0805_2012Metric_Pad1.15x1.40mm_HandSolder; Manufacturer_Part_Number MGFL2012F100MT-LF
R1: 316K; R_0603_1608Metric
R2: 110K; R_0603_1608Metric
R3, R4, R44, R45: 10K; R_0603_1608Metric
R6: 4.7k; R_0603_1608Metric
R7, R41, R42: 10k; R_0603_1608Metric
SW1: KMR231NG LFS; BTN_KMR2_4.6X2.8; Manufacturer_Part_Number KMR231NG LFS
U1: MAX706RESA; SO-8_3.9x4.9mm_P1.27mm; Manufacturer_Part_Number MAX706RESA
U2: ATSAMD51J19A-AU; QFP50P1200X1200X120-64N; Manufacturer_Part_Number ATSAMD51J19A-AU
U3: BMX160; Manufacturer_Part_Number BMX160
Y1: 32.768kHz; Crystal_SMD_3215-2Pin_3.2x1.5mm; Manufacturer_Part_Number SC-32S32.768kHz20PPM7pF

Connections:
3.3V: C5.1, C7.1, C9.2, C10.1, C11.1, C13.1, C15.1, C16.1, D1.1 (VDD), J8.1, J10.4, R3.1, R4.1, R44.1, R45.1, U1.2, U2.4 (PA03), U2.8 (VDDANA), U2.21 (VDDIO), U2.34 (VDDIO1), U2.48 (VDDIO2), U2.56 (VDDIO3), U3.5, U3.8, U3.12; also elsewhere on the board
/Avionics/BATTERY: C3.1, R1.2, R2.2, U2.15 (PA06)
/Avionics/XTAL1: C1.1, U2.1 (PA00), Y1.1
/Avionics/XTAL2: C2.1, U2.2 (PA01), Y1.2
AIN5: J10.2, U2.14 (PA05)
BURN_RELAY_A: U2.28 (PB15); also elsewhere on the board
DAC0: J10.1, U2.3 (PA02)
ENAB_BURN1: U2.60 (PB31); also elsewhere on the board
ENAB_BURN2: U2.32 (PA15); also elsewhere on the board
ENAB_GPS: U2.62 (PB01); also elsewhere on the board
ENAB_RF: U2.13 (PA04); also elsewhere on the board
FLASH_CS: U2.24 (PB11); also elsewhere on the board
FLASH_IO2: U2.19 (PA10); also elsewhere on the board
FLASH_IO3: U2.20 (PA11); also elsewhere on the board
FLASH_MISO: U2.18 (PA09); also elsewhere on the board
FLASH_MOSI: U2.17 (PA08); also elsewhere on the board
FLASH_SCK: U2.23 (PB10); also elsewhere on the board
GND: C1.2, C2.2, C3.2, C4.1, C5.2, C7.2, C9.1, C10.2, C11.2, C12.1, C13.2, C14.2, C15.2, C16.2, D1.3 (VSS), H1.1, H2.1, H3.1, H4.1, J8.2, J10.3, R2.1, R7.1, R41.2, SW1.B (S), SW1.B' (S1), U1.3, U1.4, U2.7 (GND), U2.22 (GND1), U2.33 (GND2), U2.47 (GND3), U2.54 (GND4), U3.2, U3.3, U3.6, U3.7; also elsewhere on the board
L1_PROG: R6.1; also elsewhere on the board
MISO: J8.5, U2.31 (PA14); also elsewhere on the board
MOSI: J8.3, U2.29 (PA12); also elsewhere on the board
unnamed: C12.2, C14.1, L1.1, U2.53 (VDDCORE)
unnamed: D1.4 (DIN), U2.42 (PA21)
unnamed: L1.2, U2.55 (VSW)
unnamed: R6.2, U2.16 (PA07)
unnamed: R41.1, U3.1
unnamed: R42.2, U1.7
unnamed: U1.1, U1.8
PA16: J15.2, U2.35 (PA16); also elsewhere on the board
PA17: J15.1, U2.36 (PA17); also elsewhere on the board
PA19: J9.3, U2.38 (PA19); also elsewhere on the board
PA20: J8.8, U2.41 (PA20); also elsewhere on the board
PA22: J8.9, U2.43 (PA22); also elsewhere on the board
PB16: J9.2, U2.39 (PB16); also elsewhere on the board
PB17: J9.1, U2.40 (PB17); also elsewhere on the board
PB22: J8.7, U2.49 (PB22); also elsewhere on the board
PB23: J8.6, U2.50 (PB23); also elsewhere on the board
RF1_CS: U2.59 (PB30); also elsewhere on the board
RF1_IO0: U2.6 (PB05); also elsewhere on the board
RF1_IO4: U2.5 (PB04); also elsewhere on the board
RF1_RST: U2.61 (PB00); also elsewhere on the board
RF2_CS: U2.12 (PB09); also elsewhere on the board
RF2_IO0: U2.9 (PB06); also elsewhere on the board
RF2_IO4: U2.10 (PB07); also elsewhere on the board
RF2_RST: U2.27 (PB14); also elsewhere on the board
RX: U2.64 (PB03); also elsewhere on the board
SCK: J8.4, U2.30 (PA13); also elsewhere on the board
SCL: R45.2, U2.26 (PB13); also elsewhere on the board
SCL_IMU: U3.13; also elsewhere on the board
SDA: R44.2, U2.25 (PB12); also elsewhere on the board
SDA_IMU: U3.14; also elsewhere on the board
SD_CS: U2.51 (PA27); also elsewhere on the board
SWCLK: R4.2, U2.57 (PA30); also elsewhere on the board
SWDIO: U2.58 (PA31); also elsewhere on the board
TX: U2.63 (PB02); also elsewhere on the board
USB_D+: U2.46 (PA25); also elsewhere on the board
USB_D-: U2.45 (PA24); also elsewhere on the board
VBATT: R1.1; also elsewhere on the board
VBUS_RESET: U2.37 (PA18); also elsewhere on the board
WDT_WDI: R7.2, U1.6, U2.44 (PA23)
~CHRG: U2.11 (PB08); also elsewhere on the board
~RESET: C4.2, R3.2, R42.1, SW1.A, SW1.A' (P1), U2.52 (RESETN); also elsewhere on the board

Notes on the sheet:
IMU
External Watch-Dog Timer
DECOUPLING
JTAG
RESET
PRIMARY PROCESSOR
Breakout Pins
Mounting Holes
Avionics
I2C ADDR
0x68
WDT enabled when installed
TCK TMS
NOTE: Components labeled "do not install" (DNI) are not populated by default
PCC D[0]-D[8]
SCL2
SDA2

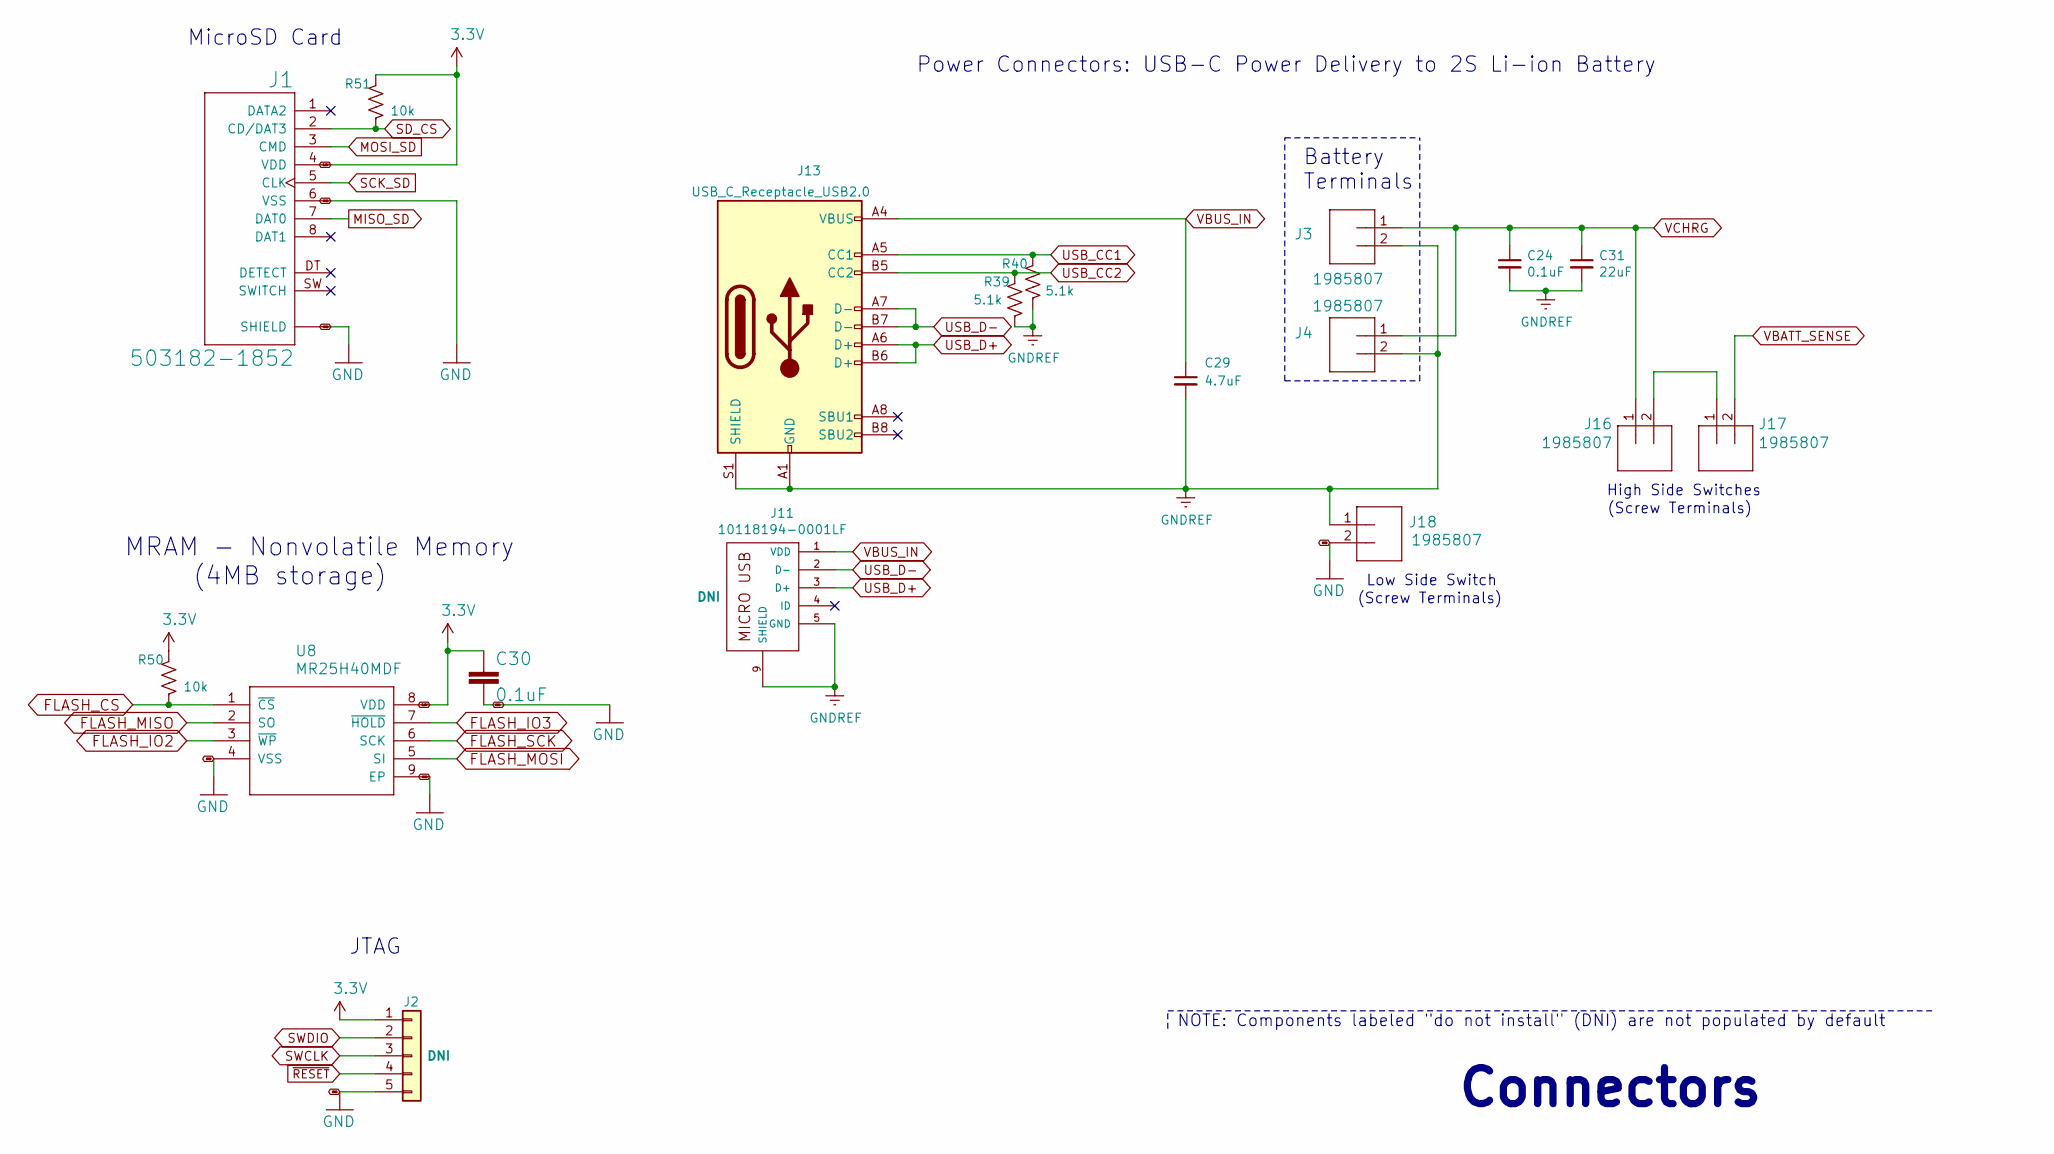
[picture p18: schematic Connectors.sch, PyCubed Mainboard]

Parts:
C24, C30: 0.1uF; C_0603_1608Metric
C29: 4.7uF; C_0603_1608Metric
C31: 22uF; C_0603_1608Metric
J1: 503182-1852; MOLEX_503182-1852; Manufacturer_Part_Number 5031821852
J2: Conn_01x05; PinHeader_1x05_P2.54mm_Vertical
J3, J4, J16, J17, J18: 1985807; SCREWTERMINAL-3.5MM-2_LOCK; Manufacturer_Part_Number 1985807
J11: 10118194-0001LF
J13: USB_C_Receptacle_USB2.0; USB_C_Receptacle_XKB_U262-161N-4BVC11; Manufacturer_Part_Number U262-161N-4BVC11
R39, R40: 5.1k; R_0603_1608Metric
R50, R51: 10k; R_0603_1608Metric
U8: MR25H40MDF; SON127P600X500X90-9N; Manufacturer_Part_Number W25Q80DVSNIG

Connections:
3.3V: C30.1, J1.4 (VDD), J2.1, R50.2, R51.2, U8.8 (VDD); also elsewhere on the board
FLASH_CS: R50.1, U8.1 (~CS); also elsewhere on the board
FLASH_IO2: U8.3 (~WP); also elsewhere on the board
FLASH_IO3: U8.7 (~HOLD); also elsewhere on the board
FLASH_MISO: U8.2 (SO); also elsewhere on the board
FLASH_MOSI: U8.5 (SI); also elsewhere on the board
FLASH_SCK: U8.6 (SCK); also elsewhere on the board
GND: C30.2, J1.6 (VSS), J1.P1 (SHIELD), J1.P2 (SHIELD), J1.P3 (SHIELD), J1.P4 (SHIELD), J1.P5 (SHIELD), J2.5, J18.2, U8.4 (VSS), U8.9 (EP); also elsewhere on the board
GNDREF: C24.2, C29.2, C31.2, J3.2, J4.2, J11.5 (GND), J11.8, J11.9 (SHIELD), J13.A1 (GND), J13.A12 (GND), J13.B1 (GND), J13.B12 (GND), J13.S1 (SHIELD), J18.1, R39.1, R40.1; also elsewhere on the board
MISO_SD: J1.7 (DAT0); also elsewhere on the board
MOSI_SD: J1.3 (CMD); also elsewhere on the board
unnamed: J16.2, J17.1
SCK_SD: J1.5 (CLK); also elsewhere on the board
SD_CS: J1.2 (CD/DAT3), R51.1; also elsewhere on the board
SWCLK: J2.3; also elsewhere on the board
SWDIO: J2.2; also elsewhere on the board
USB_CC1: J13.A5 (CC1), R40.2
USB_CC2: J13.B5 (CC2), R39.2
USB_D+: J11.3 (D+), J13.A6 (D+), J13.B6 (D+); also elsewhere on the board
USB_D-: J11.2 (D-), J13.A7 (D-), J13.B7 (D-); also elsewhere on the board
VBATT_SENSE: J17.2; also elsewhere on the board
VBUS_IN: C29.1, J11.1 (VDD), J13.A4 (VBUS), J13.A9 (VBUS), J13.B4 (VBUS), J13.B9 (VBUS); also elsewhere on the board
VCHRG: C24.1, C31.1, J3.1, J4.1, J16.1; also elsewhere on the board
~RESET: J2.4; also elsewhere on the board

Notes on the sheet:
High Side Switches
Battery Terminals
JTAG
Power Connectors: USB-C Power Delivery to 2S Li-ion Battery
MicroSD Card
MRAM - Nonvolatile Memory (4MB storage)
Connectors
Low Side Switch
NOTE: Components labeled "do not install" (DNI) are not populated by default
(Screw Terminals)

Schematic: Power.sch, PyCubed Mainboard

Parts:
C6, C22, C35, C39, C43: 10uF; C_0603_1608Metric
C17, C18, C28, C37, C38: 22uF; C_0603_1608Metric
C19, C20: 100uF; C_1210_3225Metric
C21, C45: 0.1uF; C_0603_1608Metric
C23: 2.2uF; C_0603_1608Metric
C25: 22nF; C_0603_1608Metric
C26, C32: 3.3nF; C_0603_1608Metric
C27, C33: 1uF; C_0603_1608Metric
C34: 4.7uF; C_0603_1608Metric
C36: 47nF; C_0603_1608Metric
D2: DFLS130L; PWRDI-123; Manufacturer_Part_Number DFLS130L-7
D5: GREEN LED; LED_0603_1608Metric; Manufacturer_Part_Number LTST-C190KGKT
J14: Conn_01x06; PinHeader_1x06_P2.54mm_Vertical
JP6, JP7: Jumper_3_Bridged12; SolderJumper-3_P1.3mm_Bridged12_RoundedPad1.0x1.5mm
L2: 3.3uH; L_2141; Manufacturer_Part_Number HPC5040NF-3R3MTH
L3: 33uH; L_1812_4532Metric; Manufacturer_Part_Number SNR5040K-330M
L4: 1uH; L_2510; Manufacturer_Part_Number MCS25GD-1R0MMP
Q1: IRLML2803; SOT-23; Manufacturer_Part_Number IRLML2803TRPbF
Q2, Q3: MBT2222ADW1T1; SOT-363_SC-70-6; Manufacturer_Part_Number MBT2222ADW1T1G
Q22: NDS8434; Manufacturer_Part_Number NDS8434
R8: 0.1; R_2512_6332Metric
R9: 107K; R_0603_1608Metric
R10: 0; R_0603_1608Metric
R11: 787K; R_0603_1608Metric
R12: 121K; R_0603_1608Metric
R13, R29: 73.2K; R_0603_1608Metric
R14: 22.1K; R_0603_1608Metric
R15, R30, R49: 100K; R_0603_1608Metric
R16: 845K; R_0603_1608Metric
R17, R18: 100k; R_0603_1608Metric
R19: 2.1M; R_0603_1608Metric
R20: 3.01K; R_0603_1608Metric
R21, R31, R46, R52, R55: 10K; R_0603_1608Metric
R22: 4.7K; R_0603_1608Metric
R23, R59: 3.3K; R_0603_1608Metric
R26: 1K; R_0603_1608Metric
R34: 5.23K; R_0603_1608Metric
R35: 30.1K; R_0603_1608Metric
R36: 3.16K; R_0603_1608Metric
R47: 200K; R_0603_1608Metric
R110: 20K; R_0603_1608Metric
U4: ADM1176-1ARMZ-R7; Manufacturer_Part_Number ADM1176-1ARMZ-R7
U5: TPS54226PWPRPWP14_2P31X2P46-L; PWP14_2P31X2P46-L; Manufacturer_Part_Number TPS54226PWPR
U6: LTC4121; QFN-16-PAD; Manufacturer_Part_Number LTC4121EUD
U7: KF50BD-TR; SOIC127P600X175-8N; Manufacturer_Part_Number KF50BD-TR
U17: BQ25883RGER; QFN50P400X400X100-25N-D; Manufacturer_Part_Number BQ25883RGER
U21: TPS7A4501DCQT; Manufacturer_Part_Number TPS7A4501DCQT

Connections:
3.3V: C17.2, C18.2, JP6.3 (B), JP7.3 (B), L2.2, Q22.1, Q22.2, Q22.3, R13.2, R17.2, R18.2, R23.1, U5.1 (VO); also elsewhere on the board
/Power/3V3_EN: Q2.6 (C1), R29.2, U5.7 (EN)
/Power/REGN: C34.1, R31.2, U17.11
/Power/VCHRG_IN: C22.1, D2.C, R10.2, R11.2, U6.P$3
/Power/V_RF: C43.2, JP6.1 (A), JP7.1 (A), R55.1, U7.1, U21.4
ENAB_GPS: R21.1, R22.1; also elsewhere on the board
ENAB_RF: U7.5, U21.1; also elsewhere on the board
GND: C17.1, C18.1, C19.2, C20.2, C22.2, C23.2, C26.2, C27.2, C28.2, C32.1, C43.1, C45.1, J14.5, Q1.2 (S), Q2.1 (E1), Q2.4 (E2), Q3.1 (E1), Q3.4 (E2), R9.2, R12.1, R14.1, R20.1, R21.2, R59.2, U4.4, U5.5 (GND), U5.8 (PGND1), U5.9 (PGND2), U5.15 (EPAD), U6.P$5, U6.P$7, U6.P$12, U6.P$17, U7.2, U7.3, U7.6, U7.7, U21.3, U21.6; also elsewhere on the board
GNDREF: C33.1, C34.2, C35.1, C37.1, C38.1, C39.1, J14.6, R35.1, R36.1, R46.1, U17.19, U17.20, U17.25; also elsewhere on the board
GPS_PWR_IN: Q22.5, Q22.6, Q22.7, Q22.8; also elsewhere on the board
L1_PROG: R20.2, U6.P$13; also elsewhere on the board
unnamed: C6.1, Q3.3 (C2), Q3.6 (C1), R49.2
unnamed: C6.2, Q2.5 (B2), R47.2
unnamed: C21.1, L2.1, U5.10 (SW1), U5.11 (SW2)
unnamed: C21.2, U5.12 (VBST)
unnamed: C23.1, U6.P$1
unnamed: C25.1, U6.P$2
unnamed: C25.2, L3.2, U6.P$4
unnamed: C26.1, U5.4 (SS)
unnamed: C27.1, R15.2, U5.3 (VREG5)
unnamed: C32.2, U4.5
unnamed: C35.2, L4.1, U17.21, U17.22
unnamed: C36.1, L4.2, U17.17, U17.18
unnamed: C36.2, U17.12
unnamed: C37.2, C38.2, J14.1, U17.15, U17.16
unnamed: C39.2, J14.3, U17.13, U17.14
unnamed: D5.2 (A), R31.1
unnamed: L3.1, U6.P$8
unnamed: Q1.1 (G), R22.2
unnamed: Q1.3 (D), Q22.4, R23.2
unnamed: Q2.2 (B1), Q2.3 (C2), R30.2, R110.2
unnamed: Q3.2 (B1), R110.1
unnamed: Q3.5 (B2), R52.1
unnamed: R9.1, R10.1, U6.P$16
unnamed: R11.1, R12.2, U6.P$6
unnamed: R13.1, R14.2, U5.2 (VFB)
unnamed: R15.1, U5.6 (PG)
unnamed: R16.1, U6.P$11
unnamed: R16.2, R19.2, U6.P$10
unnamed: R18.1, U6.P$15
unnamed: R26.2, U4.3
unnamed: R36.2, U17.8
unnamed: R55.2, R59.1, U21.5
SCL_PWR: U4.6, U17.5; also elsewhere on the board
SDA_PWR: U4.7, U17.4; also elsewhere on the board
STAT: D5.1 (K), U17.2
THM: R34.2, R35.2, R46.2, U17.7
USB_D+: U17.24; also elsewhere on the board
USB_D-: U17.1; also elsewhere on the board
VBATT: C19.1, C20.1, C28.1, C45.2, J14.2, R8.1, R19.1, R26.1, R29.1, R30.1, R47.1, R49.1, U4.2, U5.13 (VIN), U5.14 (VCC), U6.P$9, U7.8, U21.2; also elsewhere on the board
VBATT_SENSE: R8.2, U4.1; also elsewhere on the board
VBUS_IN: C33.2, R34.1, U17.23; also elsewhere on the board
VBUS_RESET: R52.2; also elsewhere on the board
VCC_RF1: JP6.2 (C); also elsewhere on the board
VCC_RF2: JP7.2 (C); also elsewhere on the board
VCHRG: J14.4; also elsewhere on the board
VSOLAR: D2.A; also elsewhere on the board
~CHRG: R17.1, U6.P$14; also elsewhere on the board

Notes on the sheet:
GPS Power
Regulator - 3.3V OUT
VBATT 4.5 to 18V
L1_PROG monitors charge current using: Ichrg=988*Vprog/Rprog 3.01K = 400mA max charge current
USB (Boost) Charging for 2-cell Li-Ion
Addr: 0x94
Power
Populating R9=107K,R10=464K sets turn-on voltage to 12V (solar input). Use this to tune efficiency
Vfloat=8.4V (2S Li-ion)
"VUSB"
VSOLAR 9V to 40V
Current Sense Resistor: 1.0 Ohm is about 0.3mW power lost as heat
NOTE: Components labeled "do not install" (DNI) are not populated by default
Input Current Limit Max input current (IINMAX)=KILIM/RILIM KILIM = 1098 to 1276 at most IINMAX=400mA=3.16 kohm
Sets EN low dwell time
"One Shot" Regulator Reset
Battery Power Monitor
"VCHRG"
"GND"
RBF Jumpers
Add jumper to allow USB battery charging (even inside P-Pod).
Add jumper to allow USB to power the board (even inside P-Pod).
Remove both jumpers before flight to remove risk of unknown BQ25883 radiation failure modes
MPPT=75% Voc R11=787K, R12=121K To disable MPTT: R11=10k; R12=DNI
MPPT on by default
2S Li-Ion Battery Solar Charging Circuit
RF Regulator
Radio VDD Select
Set RF Voltage: VOUT=1.21*(1+R55/R59)+(3E-6*R55) VOUT=5V (R55=10K, R59=3.3K)
Alternative RF Regulator B/C of 2021 Chip Shortage
LOW = enabled Opposite polarity than other RF reg..
Value is convenient, not necessary. 10K-80K would also work for R29

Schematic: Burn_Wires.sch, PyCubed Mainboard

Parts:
D4: DFLS130L; PWRDI-123; Manufacturer_Part_Number DFLS130L-7
JP8, JP9, JP10, JP11, JP12, JP13, JP14, JP15: Conn_01x03; MOLEX-1X3_LOCK; Manufacturer_Part_Number 22-23-2037
Q4: IRLML2803; SOT-23; Manufacturer_Part_Number IRLML2803TRPbF
Q5: IRLML2803; SOT-23; Manufacturer_Part_Number MMBT2222AT
Q6: MMBT2222AT; SOT-23; Manufacturer_Part_Number MMBT2222ALT1G
Q20, Q21: NDS8434; Manufacturer_Part_Number NDS8434
R25, R27, R28: 10k; R_0603_1608Metric
R32, R33: 4.7k; R_0603_1608Metric
R37, R38: 100k; R_0603_1608Metric
U16: PE014006; RELAY_PE014006; Manufacturer_Part_Number PE014006 TE

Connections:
/Burn Wires/VBURN1: JP11.3, Q20.5, Q20.6, Q20.7, Q20.8
/Burn Wires/VBURN2: JP12.3, Q21.5, Q21.6, Q21.7, Q21.8
/Burn Wires/VBURN_A_IN: Q20.1, Q20.2, Q20.3, Q21.1, Q21.2, Q21.3, R37.2, R38.2, U16.11
BURN_RELAY_A: Q6.1, R25.1; also elsewhere on the board
ENAB_BURN1: R27.1, R32.2; also elsewhere on the board
ENAB_BURN2: R28.1, R33.2; also elsewhere on the board
GND: JP8.1, JP9.1, JP10.1, JP11.1, JP12.1, JP13.1, JP14.1, JP15.1, Q4.2 (S), Q5.2 (S), Q6.2, R25.2, R27.2, R28.2, U16.12; also elsewhere on the board
unnamed: D4.A, Q6.3, U16.5 (A2)
unnamed: Q4.1 (G), R32.1
unnamed: Q5.1 (G), R33.1
unnamed: Q4.3 (D), Q20.4, R37.1
unnamed: Q5.3 (D), Q21.4, R38.1
VBATT: D4.C, U16.1 (A1), U16.14; also elsewhere on the board
VSOLAR: JP8.2, JP9.2, JP10.2, JP11.2, JP12.2, JP13.2, JP14.2, JP15.2; also elsewhere on the board

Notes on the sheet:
Power Relay A
Burn Wire Control (Antenna Depolyment)
Antenna Board Connectors
Solar Panel Connectors
Burn Wires
NOTE: Components labeled "do not install" (DNI) are not populated by default

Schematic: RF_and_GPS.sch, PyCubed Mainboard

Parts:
C44, C46: 10uF; C_0603_1608Metric
J5, J6, J7, J12: Amphenol_901-144; SMA_Amphenol_901-144_Vertical; Manufacturer_Part_Number 901-144
R5, R43: 10k; R_0603_1608Metric
R24: 10K; R_0603_1608Metric
R54, R56, R57, R58: 0; R_0805_2012Metric
U9, U10, U11, U12: XTB-40; XTB40_payload
U13: EP2W+; QFN32-5X5MM; Manufacturer_Part_Number EP2W+
U14: S1216V8; S1216_24PIN_PACKAGE
U15, U20: RFM9xBreakout; HOPERF_RFM9XW_SMD
U23: RFM98PW; RFM95PW; Manufacturer_Part_Number RFM98PW
U24: RFM98PW; RFM95PW

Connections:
3.3V: R5.1, R43.1, R54.1, R57.1, U9.9, U10.9, U11.9, U12.9, U23.9, U24.9; also elsewhere on the board
/RF and GPS/PYLD12_VDD: R54.2, R56.1, U10.11, U10.16, U12.11, U12.16
/RF and GPS/PYLD34_VDD: R57.2, R58.1, U9.11, U9.16, U11.11, U11.16
/RF and GPS/RF2_ANT: J12.1 (In), U15.9, U24.1
/RF and GPS/RF_IN: U13.4 (SUM_PORT), U14.11 (RF_IN)
GND: C44.1, C46.1, J5.2 (Ext), J6.2 (Ext), J7.2 (Ext), J12.2 (Ext), U9.8, U9.10, U9.15, U10.8, U10.10, U10.15, U11.8, U11.10, U11.15, U12.8, U12.10, U12.15, U13.1 (GND), U13.2 (GND), U13.3 (GND), U13.5 (GND), U13.6 (GND), U13.7 (GND), U13.8 (GND), U13.9 (GND), U13.10 (GND), U13.11 (GND), U13.12 (GND), U13.13 (GND), U13.14 (GND), U13.16 (GND), U13.17 (GND), U13.18 (GND), U13.19 (GND), U13.20 (GND), U13.21 (GND), U13.22 (GND), U13.23 (GND), U13.24 (GND), U13.25 (GND), U13.27 (GND), U13.28 (GND), U13.29 (GND), U13.30 (GND), U13.31 (GND), U13.32 (GND), U13.EP (GND), U14.10 (GND@10), U14.12 (GND@12), U14.13 (GND@13), U14.24 (GND@24), U15.1, U15.8, U15.10, U23.2, U23.16, U23.17, U24.2, U24.16, U24.17; also elsewhere on the board
GPS_PWR_IN: R24.2, U14.22 (V_BCKP), U14.23 (VCC); also elsewhere on the board
MISO: U9.6, U10.6, U11.6, U12.6; also elsewhere on the board
MISO_RF1: U23.10; also elsewhere on the board
MISO_RF2: U15.2, U24.10; also elsewhere on the board
MOSI: U9.4, U10.4, U11.4, U12.4; also elsewhere on the board
MOSI_RF1: U23.11; also elsewhere on the board
MOSI_RF2: U15.3, U24.11; also elsewhere on the board
unnamed: J5.1 (In), U13.15 (PORT1)
unnamed: J6.1 (In), U13.26 (PORT2)
unnamed: R24.1, U14.8 (RSTN)
PA16: U11.1, U12.23; also elsewhere on the board
PA17: U11.2, U12.22; also elsewhere on the board
PA19: U9.18, U12.7, U12.18; also elsewhere on the board
PA20: U9.7, U9.17, U10.7; also elsewhere on the board
PA22: U11.7, U12.17; also elsewhere on the board
PB16: U9.20, U12.3, U12.20; also elsewhere on the board
PB17: U9.21, U10.3; also elsewhere on the board
PB22: U11.3, U12.21; also elsewhere on the board
PB23: U9.3, U9.22, U10.2; also elsewhere on the board
RF1_ANT: J7.1 (In), U23.1
RF1_CS: R5.2, U23.13; also elsewhere on the board
RF1_IO0: U23.6; also elsewhere on the board
RF1_IO4: U23.4; also elsewhere on the board
RF1_RST: U23.14; also elsewhere on the board
RF2_CS: R43.2, U15.5, U24.13; also elsewhere on the board
RF2_IO0: U15.14, U24.6; also elsewhere on the board
RF2_IO4: U15.12, U24.4; also elsewhere on the board
RF2_RST: U15.6, U24.14; also elsewhere on the board
RX: U14.20 (TXD); also elsewhere on the board
SCK: U9.5, U10.5, U11.5, U12.5; also elsewhere on the board
SCK_RF1: U23.12; also elsewhere on the board
SCK_RF2: U15.4, U24.12; also elsewhere on the board
TX: U14.21 (RXD); also elsewhere on the board
VBATT: R56.2, R58.2; also elsewhere on the board
VCC_RF1: C44.2, U23.5; also elsewhere on the board
VCC_RF2: C46.2, U15.13, U24.5; also elsewhere on the board

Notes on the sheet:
GPS Module
RF Splitter (2 Way, 0deg DC-Pass)
Modular Radios (HopeRF format)
Radio #1
Radio, GPS, Payloads
Modular Payloads
Radio #2
NOTE: Components labeled "do not install" (DNI) are not populated by default
PAYLOAD 1
PAYLOAD 3
PAYLOAD 4
PAYLOAD 2

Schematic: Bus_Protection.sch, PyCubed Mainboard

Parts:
C8, C40, C41, C42: 10nF; C_0603_1608Metric
Q7, Q8, Q15, Q16: MBT2222ADW1T1; SOT-363_SC-70-6; Manufacturer_Part_Number MBT2222ADW1T1G
Q11: MMDT2907; SOT-363_SC-70-6; Manufacturer_Part_Number MMDT2907AQ-7-F
Q12, Q13, Q18, Q19: BSS138DWQ-7; Manufacturer_Part_Number BSS138DWQ-7
Q17: MMBT2907; SOT-23; Manufacturer_Part_Number MMBT2907ALT1G
R48, R53, R97, R98, R99, R101, R104, R107, R108, R109: 0; R_0603_1608Metric
R60, R92: 4.7k; R_0603_1608Metric
R61, R62, R66, R67, R82, R83, R84, R85: 10K; R_0603_1608Metric
R63, R64, R69, R70, R77, R78: 1K; R_0603_1608Metric
R68: 4.7K; R_0603_1608Metric
R71, R72, R86, R87: 680; R_0603_1608Metric
R73, R74, R93, R94: 100K; R_0603_1608Metric
R75, R76, R95, R96: 200K; R_0603_1608Metric

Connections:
3.3V: R61.1, R62.1, R66.1, R67.1, R73.1, R74.1, R82.1, R83.1, R84.1, R85.1, R93.1, R94.1; also elsewhere on the board
GND: C8.2, C40.2, C41.2, C42.2, Q12.1, Q12.4, Q13.1, Q13.4, Q18.1, Q18.4, Q19.1, Q19.4; also elsewhere on the board
MISO: Q11.3, Q11.6, Q17.3, R101.2, R104.2, R107.2; also elsewhere on the board
MISO_RF1: R99.2, R101.1; also elsewhere on the board
MISO_RF2: R48.2, R107.1; also elsewhere on the board
MISO_SD: R53.2, R104.1; also elsewhere on the board
MOSI: R64.2, R70.1, R77.2; also elsewhere on the board
MOSI_RF1: R70.2; also elsewhere on the board
MOSI_RF2: R77.1; also elsewhere on the board
MOSI_SD: R64.1; also elsewhere on the board
unnamed: C8.1, Q12.5, R75.2
unnamed: C40.1, Q13.5, R76.2
unnamed: C41.1, Q18.5, R95.2
unnamed: C42.1, Q19.5, R96.2
unnamed: Q7.2 (B1), R71.1
unnamed: Q8.2 (B1), R72.1
unnamed: Q11.1, R99.1
unnamed: Q11.2, R68.1
unnamed: Q11.4, R53.1
unnamed: Q11.5, R92.1
unnamed: Q12.2, Q12.3, R73.2
unnamed: Q7.5 (B2), Q12.6, R61.2, R71.2
unnamed: Q13.2, Q13.3, R74.2
unnamed: Q8.5 (B2), Q13.6, R62.2, R72.2
unnamed: Q15.2 (B1), R86.1
unnamed: Q15.5 (B2), Q18.6, R82.2, R86.2
unnamed: Q16.2 (B1), R87.1
unnamed: Q16.5 (B2), Q19.6, R83.2, R87.2
unnamed: Q17.1, R60.1
unnamed: Q17.2, R48.1
unnamed: Q18.2, Q18.3, R93.2
unnamed: Q19.2, Q19.3, R94.2
RF1_CS: R68.2; also elsewhere on the board
RF2_CS: R60.2; also elsewhere on the board
SCK: R63.2, R69.2, R78.2; also elsewhere on the board
SCK_RF1: R69.1; also elsewhere on the board
SCK_RF2: R78.1; also elsewhere on the board
SCK_SD: R63.1; also elsewhere on the board
SCL: Q7.1 (E1), Q7.3 (C2), Q15.1 (E1), Q15.3 (C2), R97.2, R108.2; also elsewhere on the board
SCL_IMU: Q7.4 (E2), Q7.6 (C1), R66.2, R75.1, R97.1; also elsewhere on the board
SCL_PWR: Q15.4 (E2), Q15.6 (C1), R84.2, R95.1, R108.1; also elsewhere on the board
SDA: Q8.1 (E1), Q8.3 (C2), Q16.1 (E1), Q16.3 (C2), R98.2, R109.2; also elsewhere on the board
SDA_IMU: Q8.4 (E2), Q8.6 (C1), R67.2, R76.1, R98.1; also elsewhere on the board
SDA_PWR: Q16.4 (E2), Q16.6 (C1), R85.2, R96.1, R109.1; also elsewhere on the board
SD_CS: R92.2; also elsewhere on the board

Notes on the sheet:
Bus Protection
NOTE: Components labeled "do not install" (DNI) are not populated by default
I2C Bus Protection - IMU
I2C Bus Protection - Power Monitor & USB Charger
SPI Bus Protection - SD Card and Payloads
SPI Bus Protection - Radio 1
SPI Bus Protection - Radio 2
Bus Protection - Bypass Jumpers
These novel bus protection circuits prevent traditional I2C/SPI failure modes where a single slave failure can disable the entire bus. Learn more: https://doi.org/10.36227/techrxiv.15166620 By default, slave clock and/or data lines can be held low and the Master (SAMD51) will still be able to commu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
NOTE

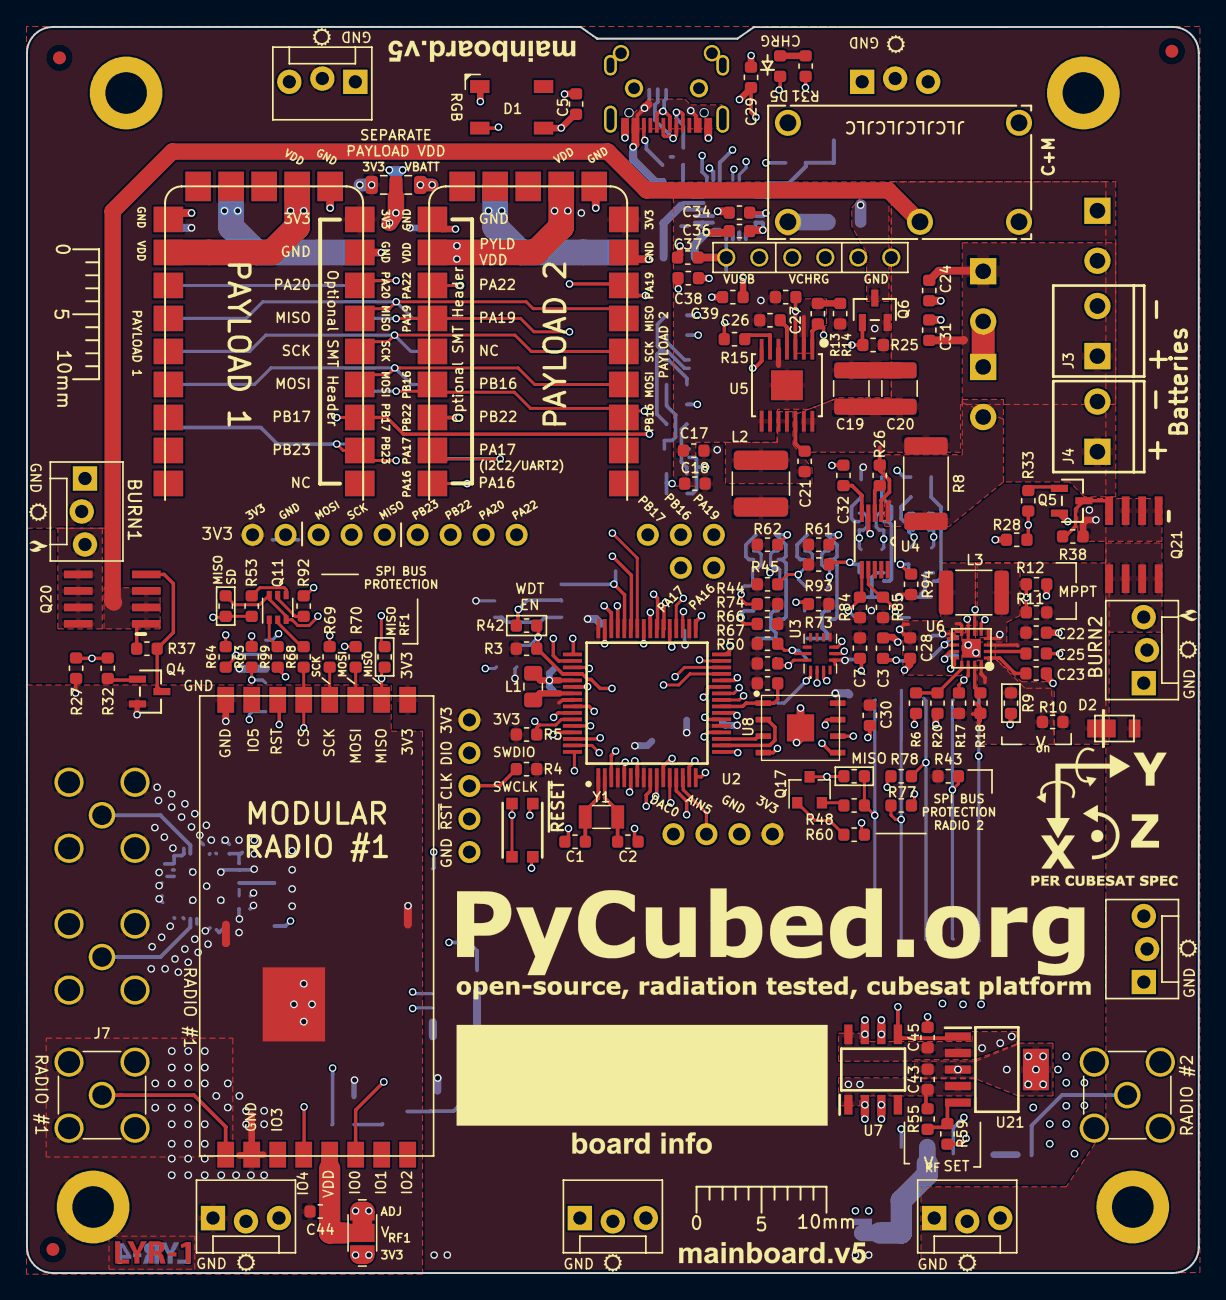
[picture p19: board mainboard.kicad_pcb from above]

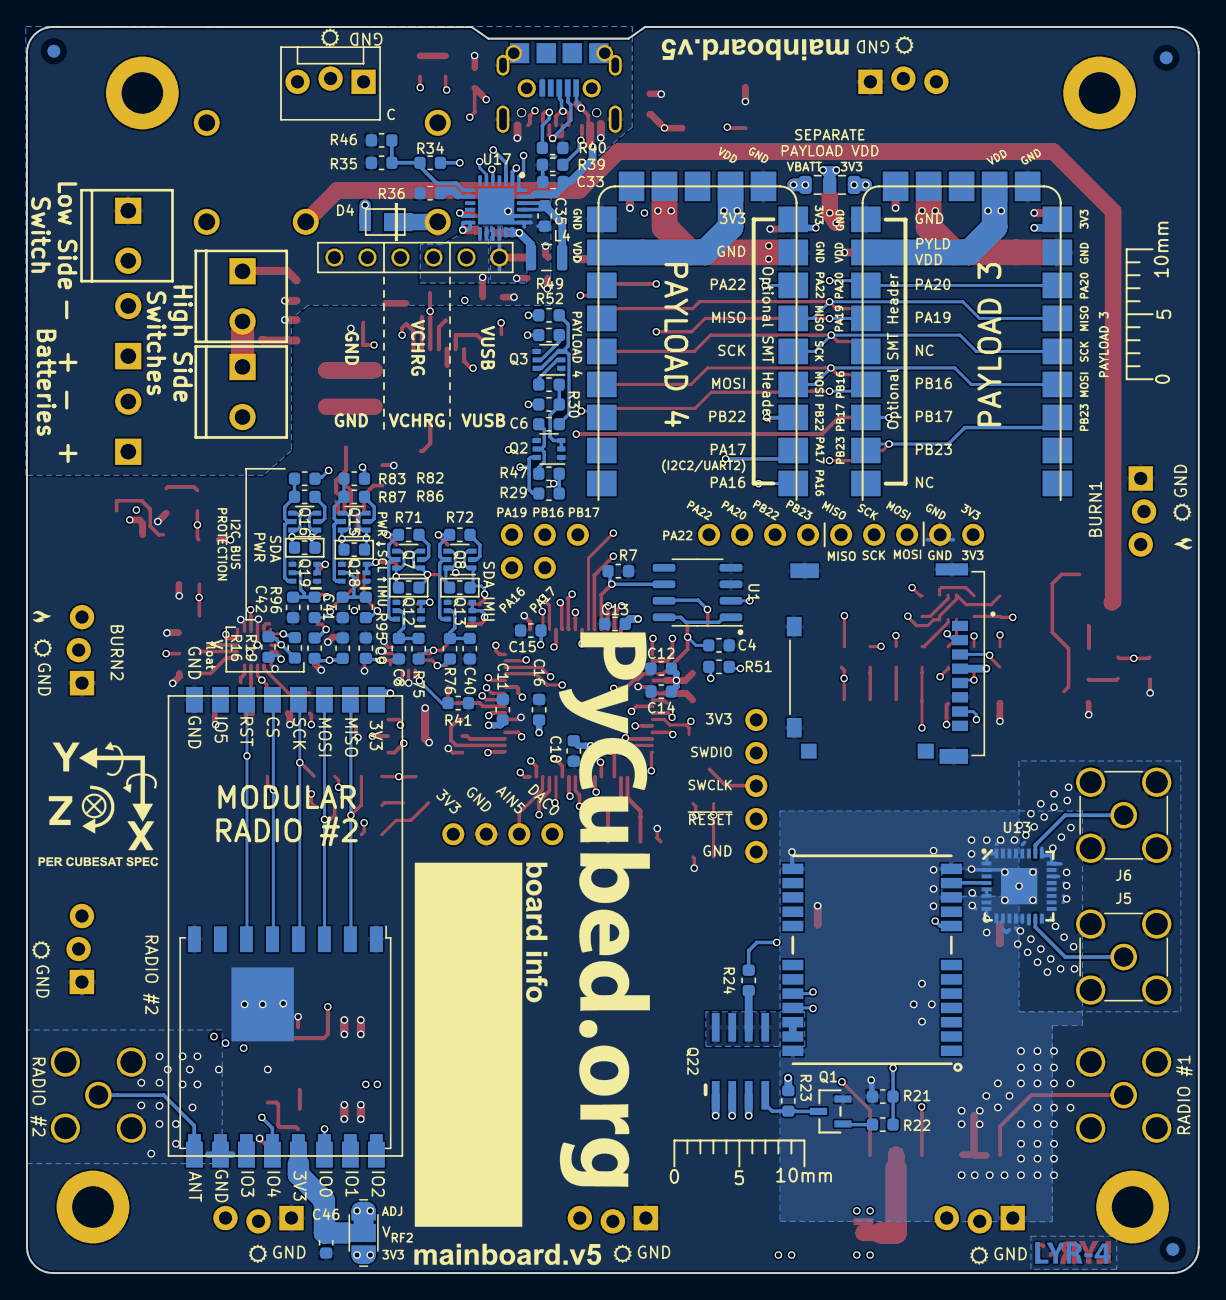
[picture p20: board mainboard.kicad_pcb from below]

Board: 4 copper layers, 90.2 x 95.9 mm, 230 parts (91 on the bottom side), 160 nets.

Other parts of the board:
REF1B, REF1T, REF2B, REF2T, REF3B, REF3T: Fiducial_1mm_Mask2mm

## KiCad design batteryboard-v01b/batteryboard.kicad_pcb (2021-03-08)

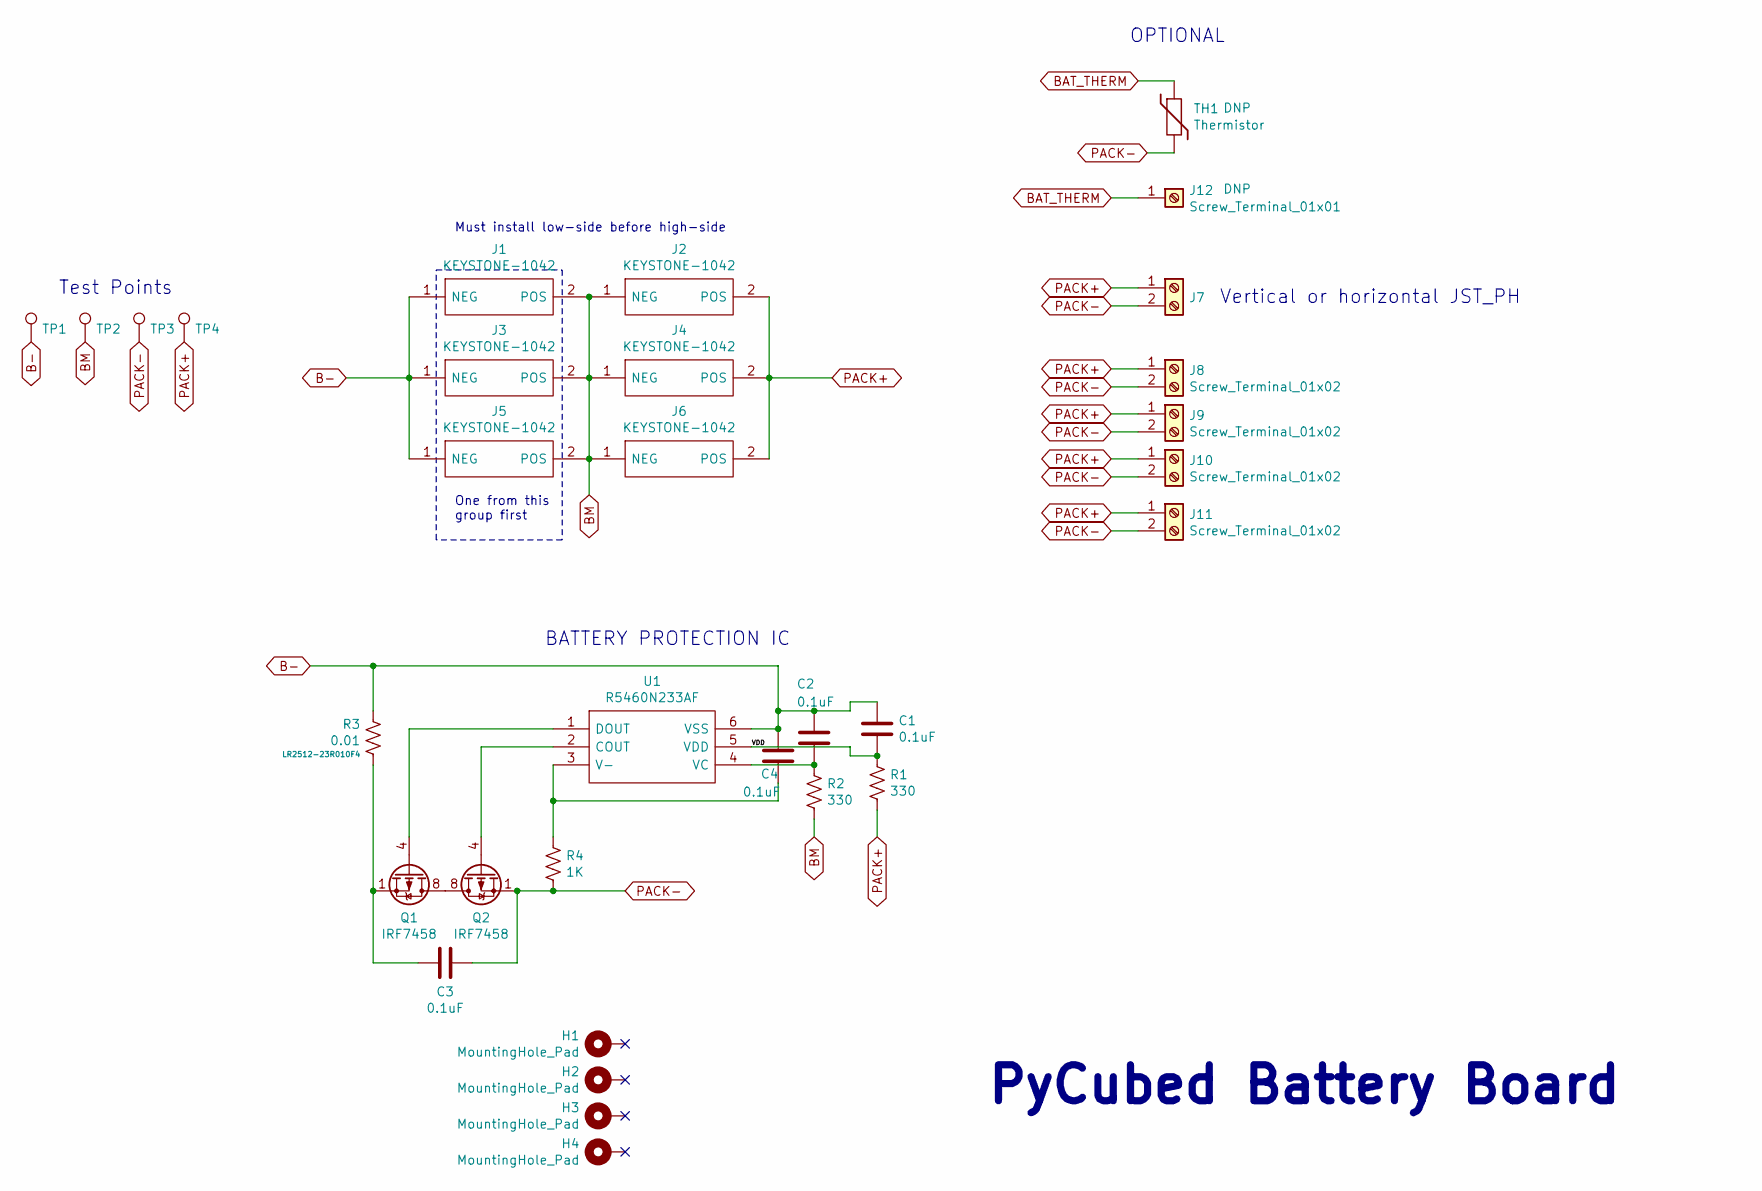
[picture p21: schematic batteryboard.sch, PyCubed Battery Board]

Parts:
C1, C2, C3, C4: 0.1uF; C_0603_1608Metric
H1, H2, H3, H4: MountingHole_Pad; MountingHole_3.2mm_M3_DIN965_PadMOD
J1, J2, J3, J4, J5, J6: KEYSTONE-1042; Manufacturer_Part_Number 1042; Mouser Part Number 534-1042
J7: JST_PH_S2B-PH-SM4; JST_PH_S2B-PH-SM4-TB_1x02-1MP_P2.00mm_Horizontal
J8, J9, J10, J11: Screw_Terminal_01x02; SCREWTERMINAL-3.5MM-2_LOCK
J12: Screw_Terminal_01x01; PinHeader_1x01_P1.00mm_Vertical
Q1, Q2: IRF7458; SOIC-8_3.9x4.9mm_P1.27mm
R1, R2: 330; R_0603_1608Metric
R3: 0.01; R_2512_6332Metric
R4: 1K; R_0603_1608Metric; Manufacturer_Part_Number LR2512-23R010F4
TH1: Thermistor; R_Axial_DIN0204_L3.6mm_D1.6mm_P5.08mm_Vertical
TP1, TP2, TP3, TP4: TestPoint; TestPoint_Loop_D1.80mm_Drill1.0mm_Beaded
U1: R5460N233AF; SOT95P280X130-6N; Manufacturer_Part_Number R5460N233AF-TR-FE; Mouser Part Number 848-R5460N233AFTRFE

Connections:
/VDD: C1.2, R1.2, U1.5 (VDD)
B-: C1.1, C2.1, C4.1, J1.1 (NEG), J3.1 (NEG), J5.1 (NEG), R3.1, TP1.1, U1.6 (VSS)
BAT_THERM: J12.1, TH1.1
BM: J1.2 (POS), J2.1 (NEG), J3.2 (POS), J4.1 (NEG), J5.2 (POS), J6.1 (NEG), R2.1, TP2.1
unnamed: C2.2, R2.2, U1.4 (VC)
unnamed: C3.1, Q1.1 (S), Q1.2 (S), Q1.3 (S), R3.2
unnamed: C4.2, R4.1, U1.3 (V-)
unnamed: Q1.4 (G), U1.1 (DOUT)
unnamed: Q1.5 (D), Q1.6 (D), Q1.7 (D), Q1.8 (D), Q2.5 (D), Q2.6 (D), Q2.7 (D), Q2.8 (D)
unnamed: Q2.4 (G), U1.2 (COUT)
PACK+: J2.2 (POS), J4.2 (POS), J6.2 (POS), J7.1, J8.1, J9.1, J10.1, J11.1, R1.1, TP4.1
PACK-: C3.2, J7.2, J8.2, J9.2, J10.2, J11.2, Q2.1 (S), Q2.2 (S), Q2.3 (S), R4.2, TH1.2, TP3.1

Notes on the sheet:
Must install low-side before high-side
One from this group first
OPTIONAL
Test Points
Vertical or horizontal JST_PH
BATTERY PROTECTION IC
PyCubed Battery Board

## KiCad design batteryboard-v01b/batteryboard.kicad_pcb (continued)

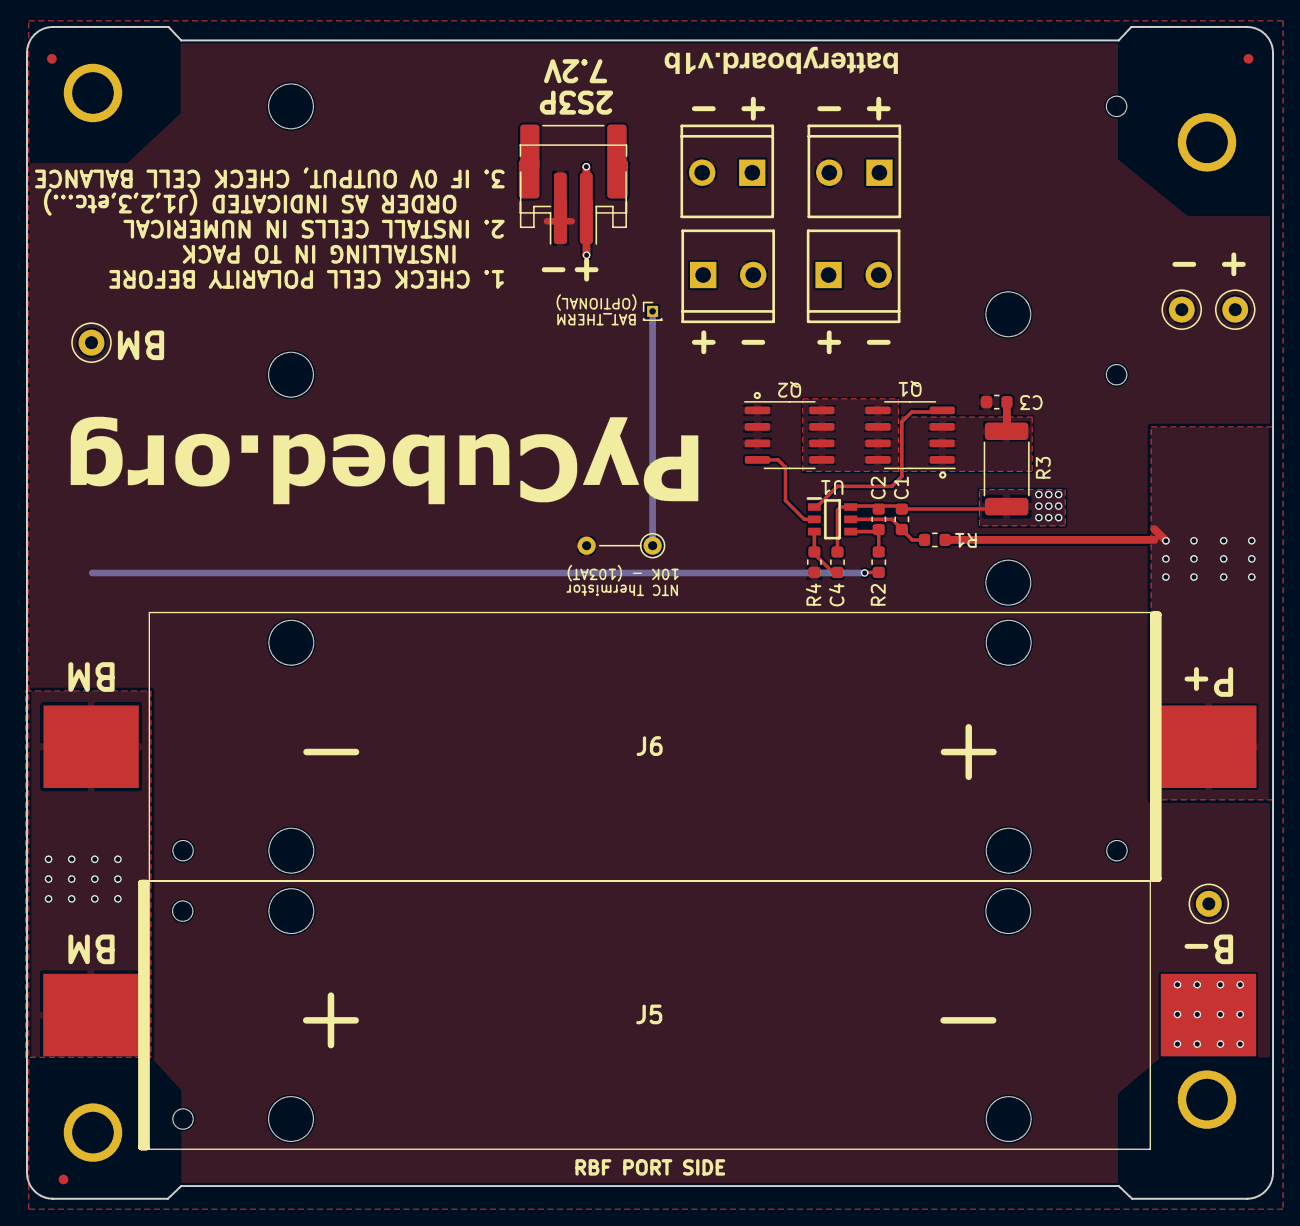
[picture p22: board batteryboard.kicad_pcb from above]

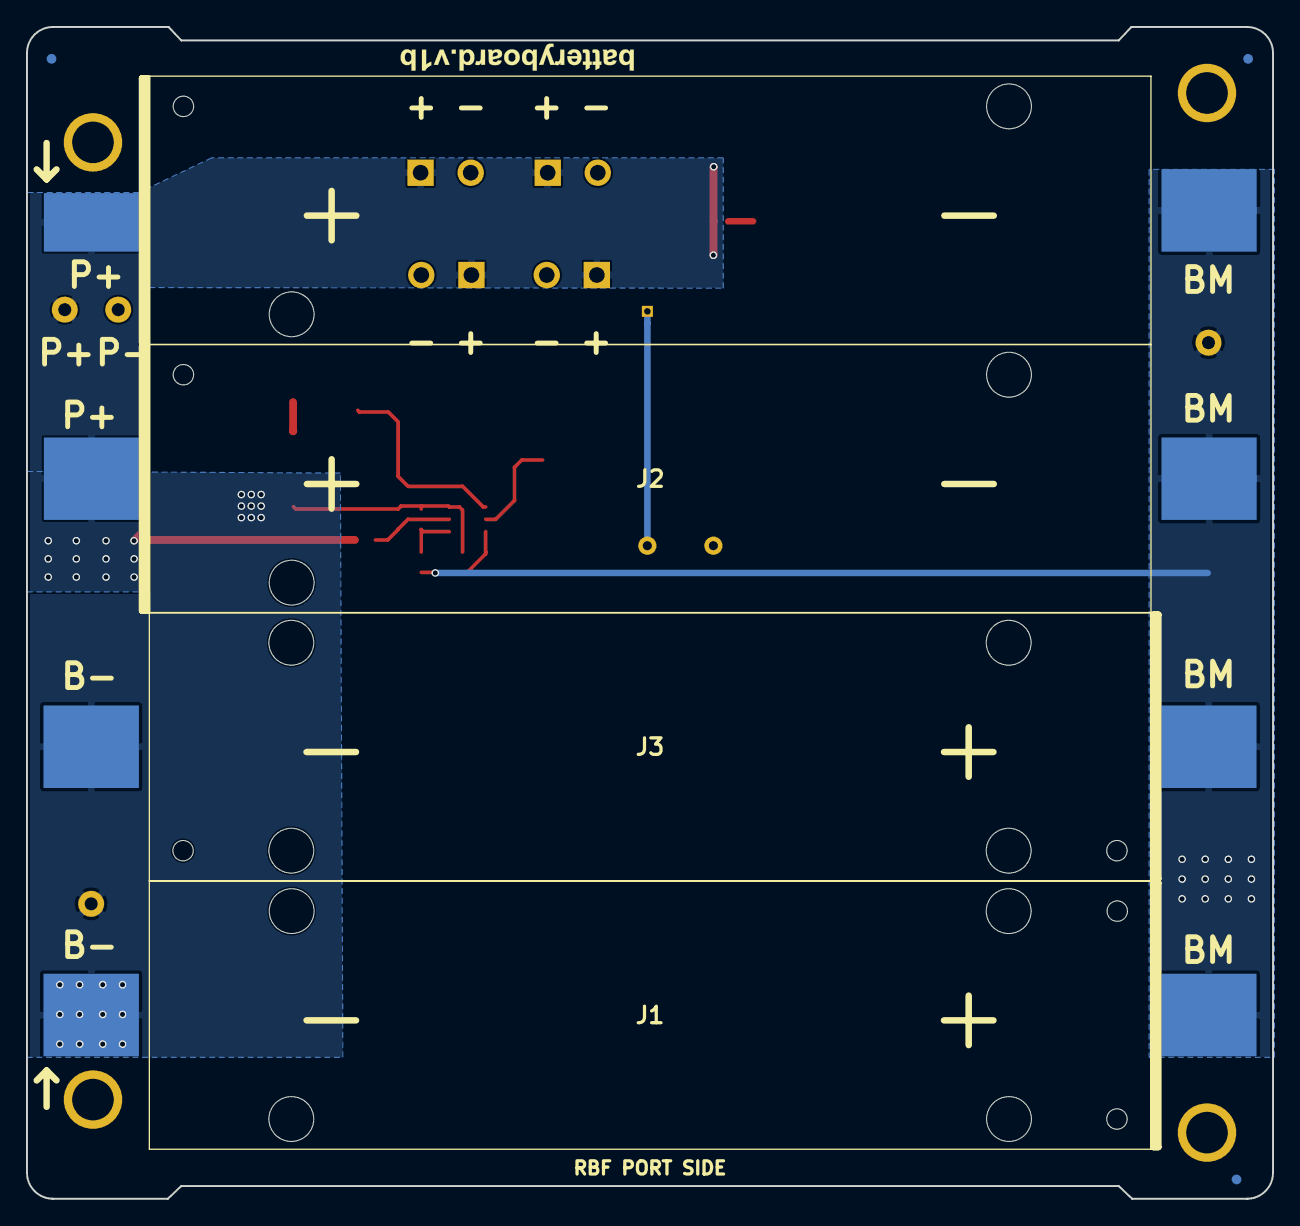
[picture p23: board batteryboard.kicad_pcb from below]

Board: 2 copper layers, 95.9 x 90.2 mm, 35 parts (5 on the bottom side), 12 nets.

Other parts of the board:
Ref**: Val**; battery_version
Ref**#2: Val**; battery_version
Ref**#3: Val**; pycubed_logo

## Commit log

2019-07-13 adding v01 hardware from KickSat and current mainboard-v02
    [Avionics.sch, Burn_Wires.sch, Connectors.sch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]
2019-07-13 adding a gitignore file for KiCad back-up files
2019-07-13 adding v01 schematic pdf
    [Avionics.sch, Connectors.sch, Power.sch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]
2019-07-13 fixing bold font and adding schematic pdf of v02
    [Avionics.sch, Burn_Wires.sch, Connectors.sch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]
2019-07-16 mainboard-v02 with RFM98PW
    [Avionics.sch, Burn_Wires.sch, Connectors.sch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]
2019-07-28 adding pcb backups to the gitignore
2019-07-28 adding interactive bom
2019-07-28 adding interactive BOM for v01 and v02
2019-07-28 adding BOM links to readme
2019-07-31 adding PyCubed board image
2019-07-31 resizing board pic
2019-12-01 adding mainboardv4 branch
    [Avionics.sch, Burn_Wires.sch, Connectors.sch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]
2020-01-10 adding mainbaordv04 layout and BOM
    [Avionics.sch, Burn_Wires.sch, Connectors.sch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]
2020-04-03 cleaned up v04
    [Avionics.sch, Burn_Wires.sch, Connectors.sch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]
2020-05-27 stovepiping battery board to master
    [batteryboard.kicad_pcb, batteryboard.sch, batteryboard.step]
2020-05-27 adding disclaimer 😇
2020-08-31 adding battery board manufacturing zip for easy ordering
2021-03-08 added battery board v01b which disconnects corner thru-holes from GND and more DNP details
    [batteryboard.kicad_pcb, batteryboard.sch, batteryboard.step]
2021-08-13 adding v05 layout & schematics
    [Avionics.sch, Burn_Wires.sch, Bus_Protection.sch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]
2021-08-13 adding interactive BOM and updating readme
2021-09-18 adding more manufacturing outputs (placement, boms, etc)
    [mainboardv05.csv]
2021-09-21 tweaking one-shot values for reduced power consumption
    [Power.sch, mainboard.kicad_pcb, mainboardv05.csv]
2021-11-10 Update README.md
    https://forum.kicad.info/t/warning-avoid-all-links-to-kicad-pcb-org-use-kicad-org/31521

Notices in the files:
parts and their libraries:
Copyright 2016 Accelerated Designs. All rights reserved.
